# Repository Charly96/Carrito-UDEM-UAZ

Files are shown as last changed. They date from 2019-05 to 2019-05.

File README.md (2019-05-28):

# Carrito-UDEM-UAZ
Instrumentación, optimización estructural  y fabricación de vehículo con capacidades de autonomía a escala de bajo costo
Las piezas disponibles en este repositorio están en formato .prt, pero las disponibles en la carpeta .ige se encuentran en ese mismo formato para poder ser utilziadas en cualquier programa de CAD. 
Si se desea ensamblar, recomiendo leer el archivo ¨Repositorio¨ el cual indica paso a paso como hacerlo además de cuáles tornillos utilizar
###############################################

# Cart-UDEM-UAZ
Instrumentation, structural optimization and vehicle manufacturing with autonomy capabilities at a low cost scale
The pieces available in this repository are in .prt format, but the ones available in the .ige folder are in that same format to be used in any CAD program.
If you want to assemble, I recommend reading the file "Repository" which indicates step by step how to do it in addition to which screws to use

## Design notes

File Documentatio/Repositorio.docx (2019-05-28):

UNIVERSIDAD DE MONTERREY

ESCUELA DE INGENIERÍA Y TECNOLOGÍAS

Repositorio para elaborar y poner en marcha vehículo a escala con capacidades autónomas.

Asesor(es):

Antonio Martínez Torteya, Ph.D.

José María Celaya Padilla, Ph.D.

Integrantes:

Mauricio Delgado Vidal 339878 IMT

Carlos Arizpe Bautista 542800 IDA

Rodrigo Antonio García García 192376 IMT

San Pedro Garza García N.L, 24 de mayo del 2019

# Introducción

En este documento explicaremos cómo se realizó este vehículo y sus características y medidas para que pueda ser replicado, o bien se podría modificar si el usuario quisiera. De igual manera explicaremos qué sensores utilizamos y recomendamos junto con sus posicionamientos, que estos también quedan al criterio del usuario para modificar si gusta

# Materiales

- 4 sensores infrarrojos keyence
- 6 sensores ultrasónicos
- 1 Raspberry pi 3 b+
- 1 cámara web
- 4 llantas marca Steren
- 2 motorreductores
- 1 puente H

## Tornillos

- Holder

Tornillo: M5 x 0.8 mm Thread, 45 mm Long ……………….X2

Tuerca: M5 x 0.8mm…………….X2

Battery Holder

Tornillo:M5x0.8mm,20mm long…….X2

Tuerca M5x0.8mm………2

- Raspberry

Tornillo: M2.5x0.45,25mm long……X2

Tuerca: M2.5x0.8mm…X2

- Motores Traseros

Tornillo: M3x0.5mm,40mm………X4

Tuerca: M3x0.5……….X4

- Base de sensores

Tornillo: M3x0.5mm,20 mm long……X14

Tuerca: M3x0.5mm,20mm log………X14

- Motor de dirección

Tornillo: M2.5,6mm long………X2

- Unión Lateral

Tornillo: M4, 6mm long….X4

# Diseño

El diseño del chasis consta de dos partes que sirven como la base donde se colocan todos los sensores, componentes electrónicos y elementos de sujeción.

En esta sección se incluirán solo los modelos creados y no los que se encontraron disponibles en Internet. Estos últimos se incluyen en otra sección más adelante.

# Dibujos mecánicos

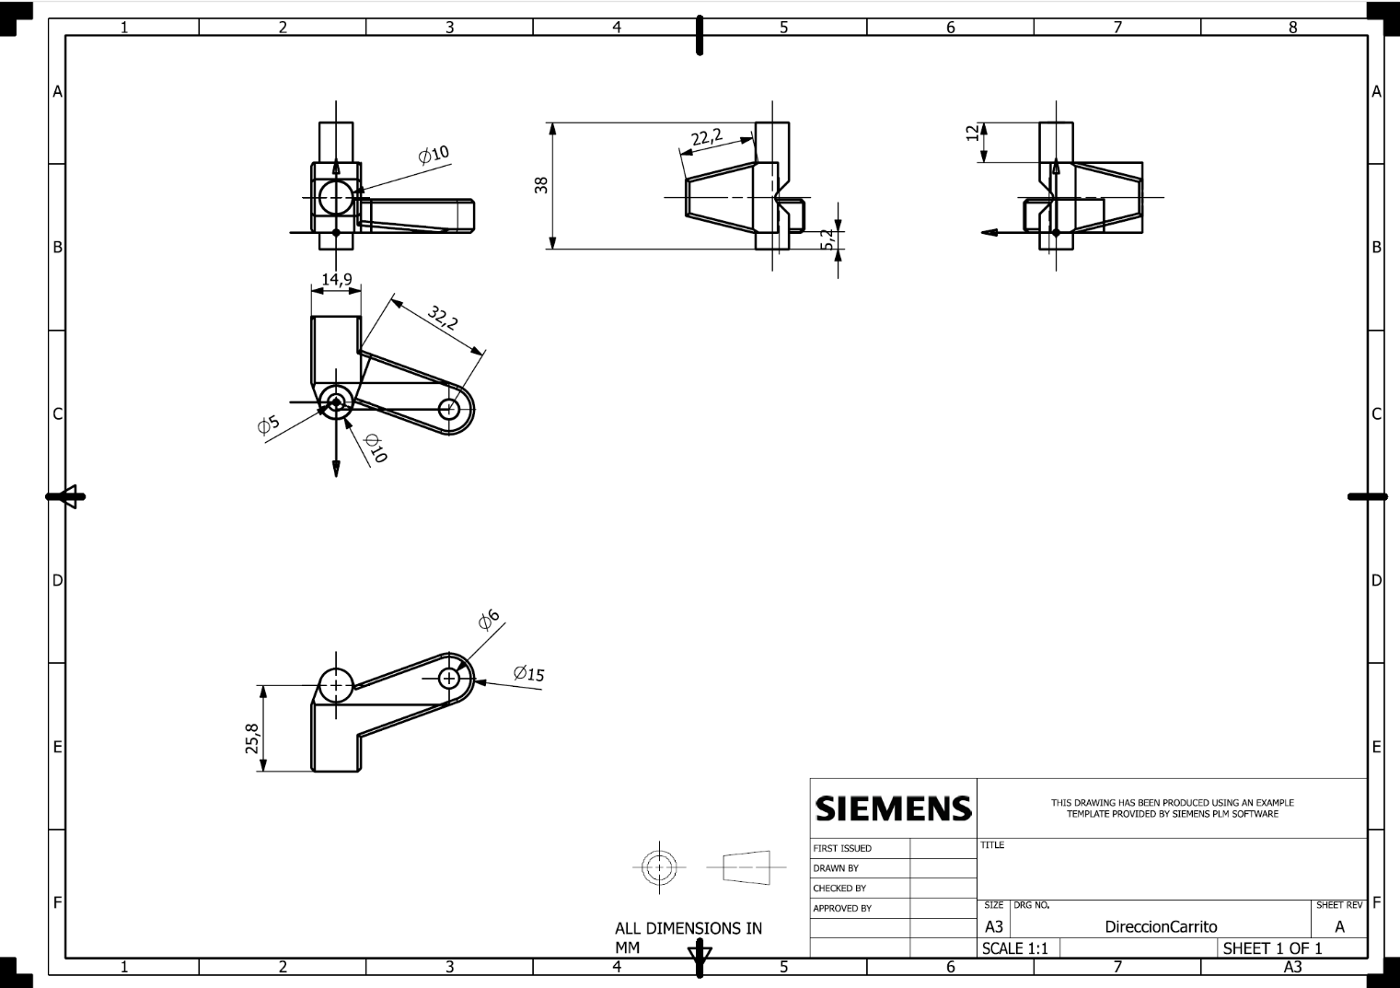
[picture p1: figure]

## Partes de Dirección

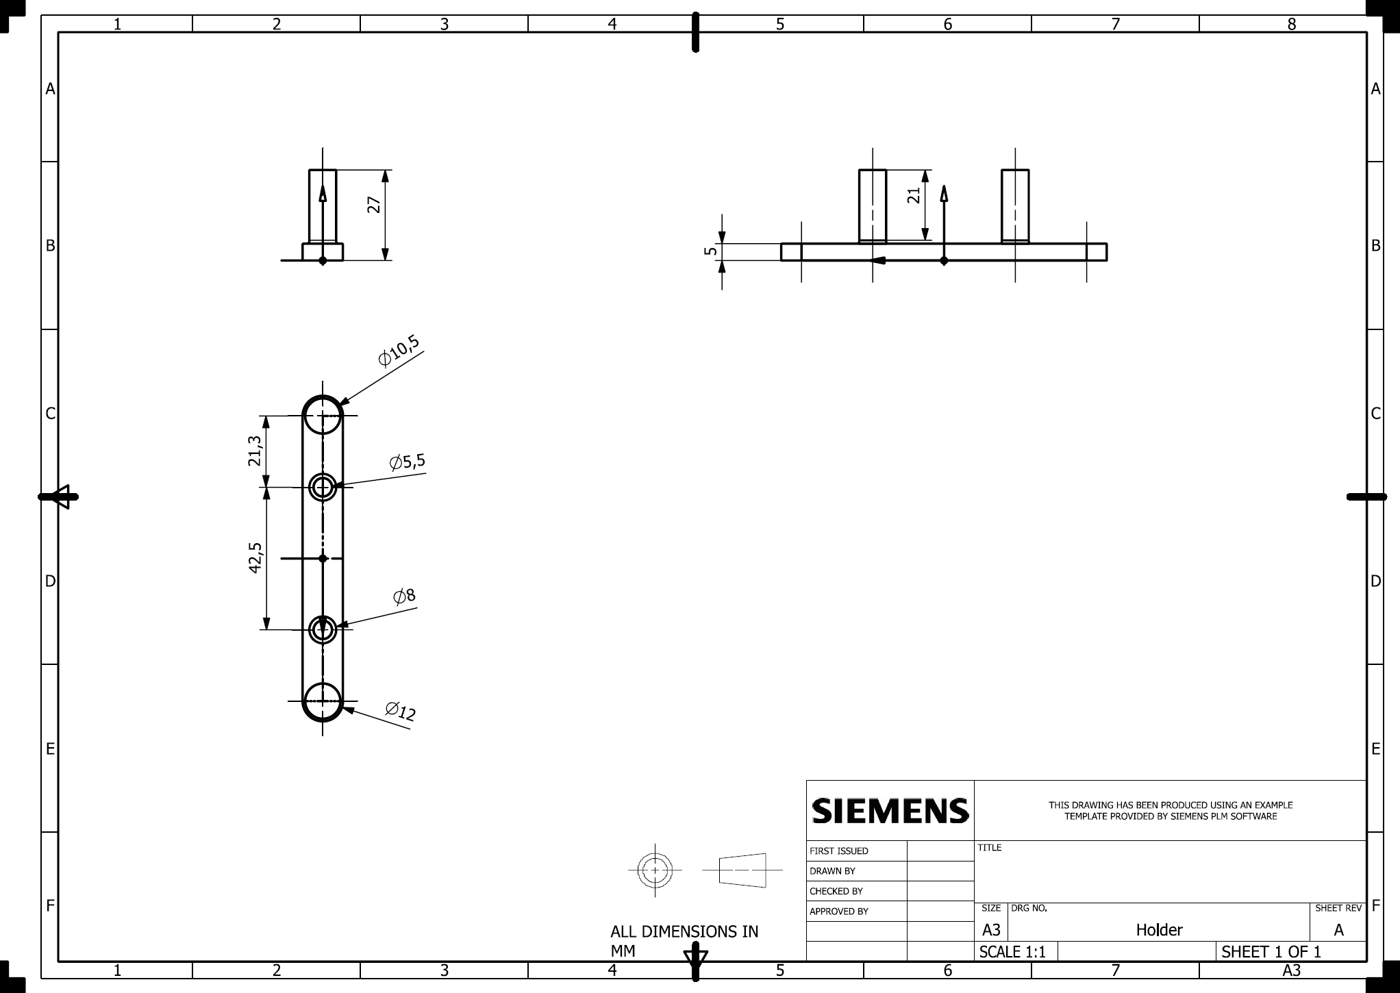
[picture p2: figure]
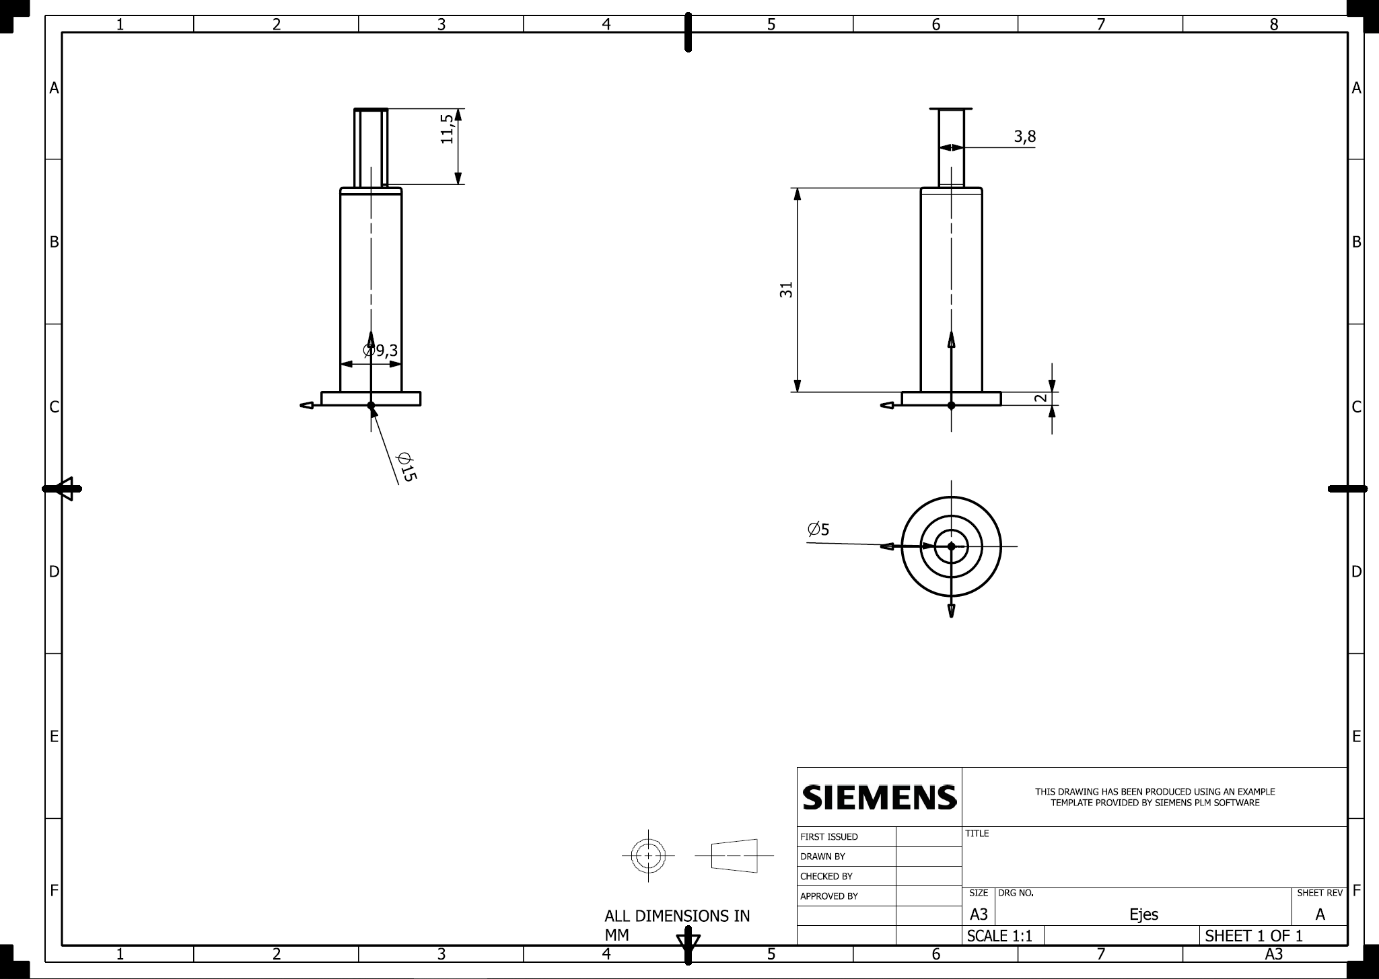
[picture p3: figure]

## Bases de sensores

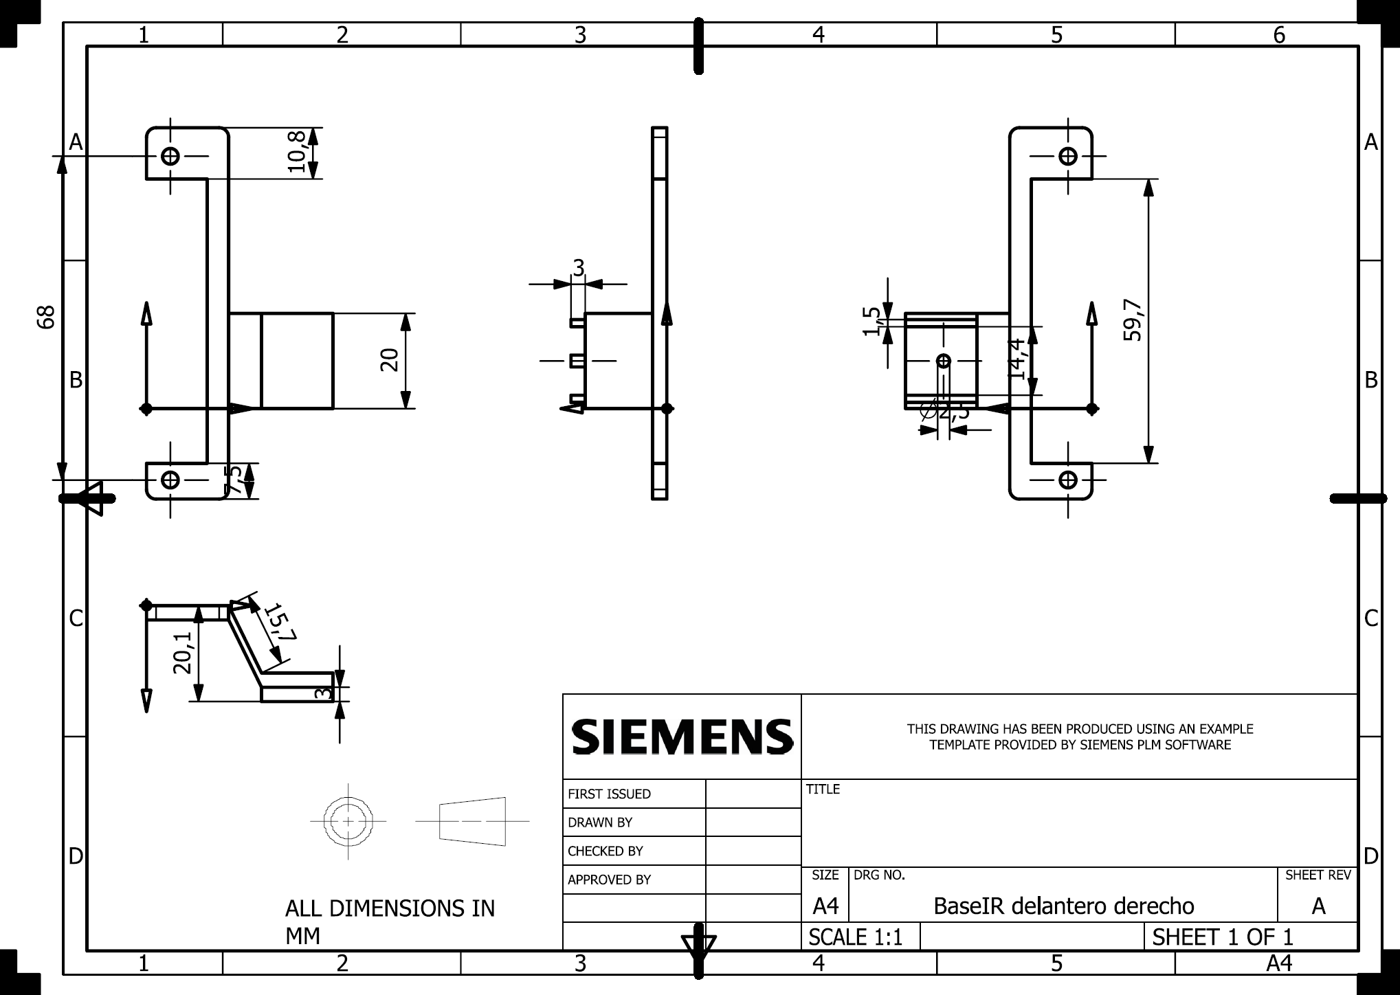
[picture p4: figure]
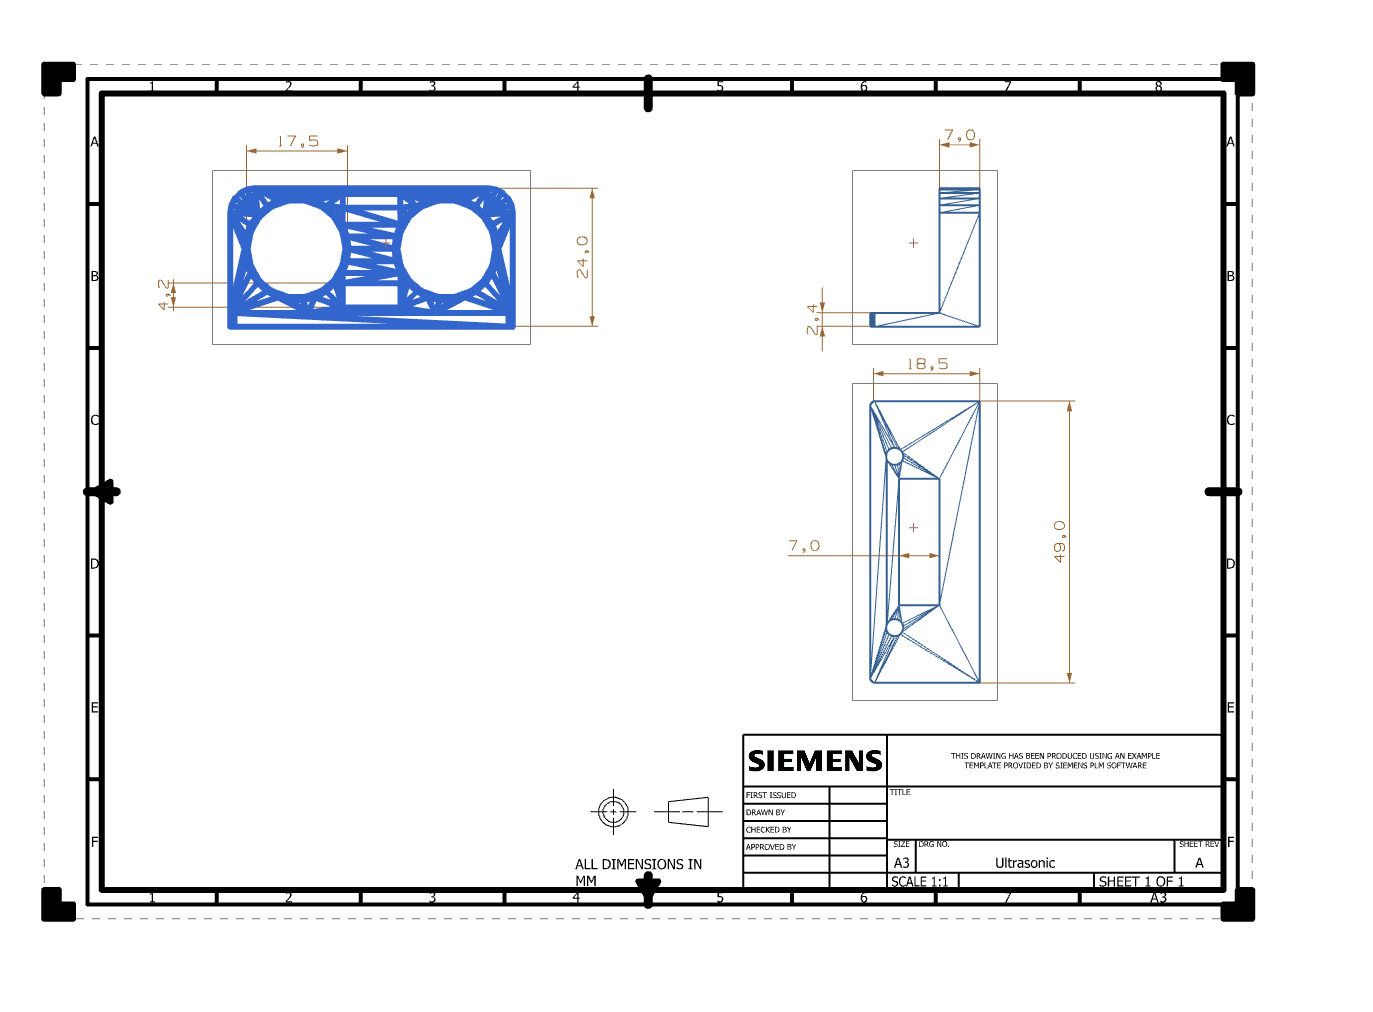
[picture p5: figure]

## Chasis

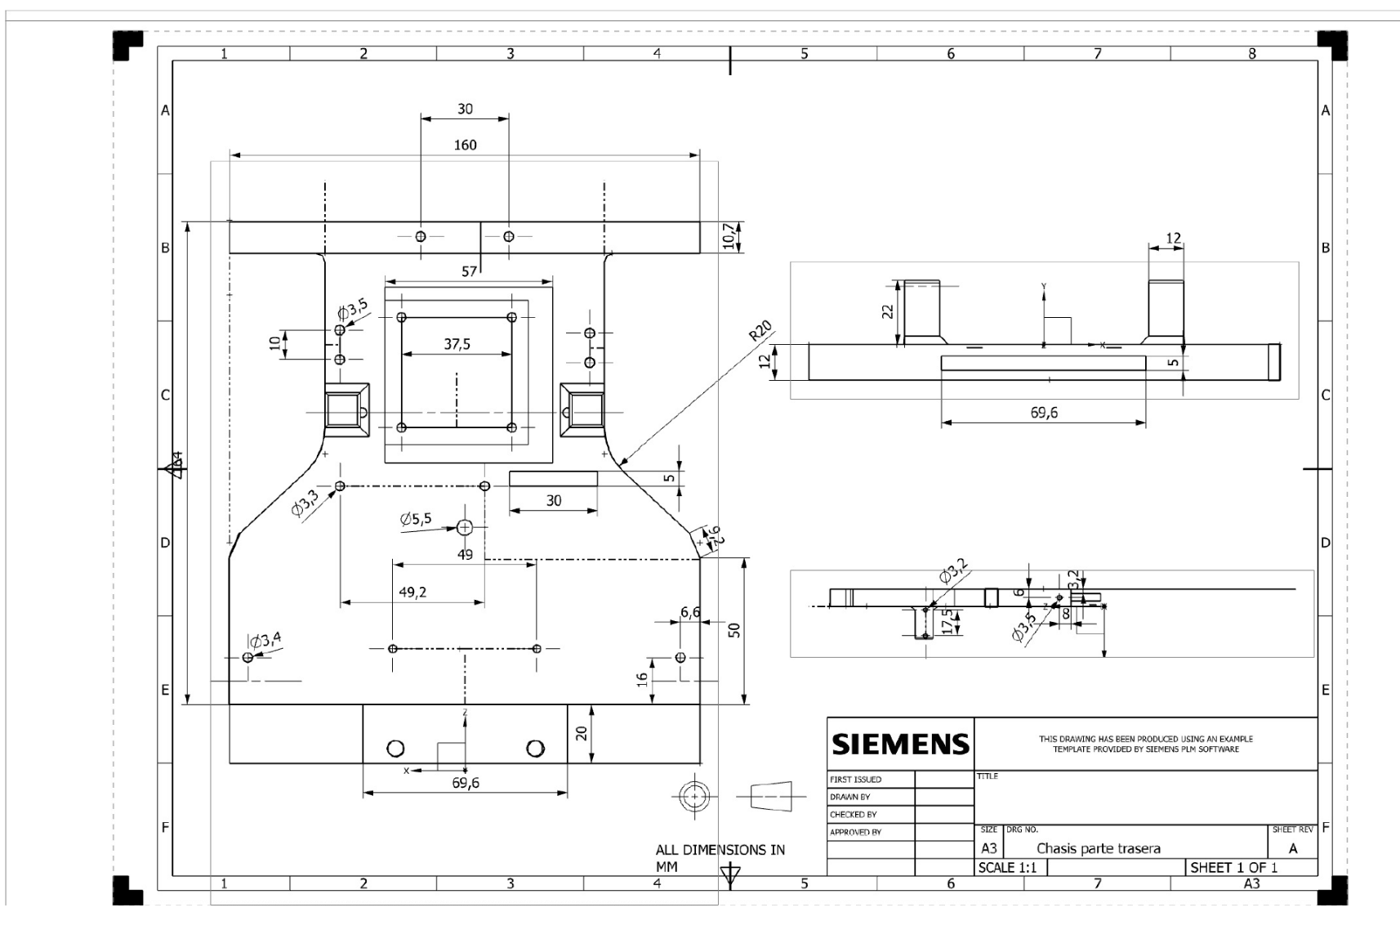
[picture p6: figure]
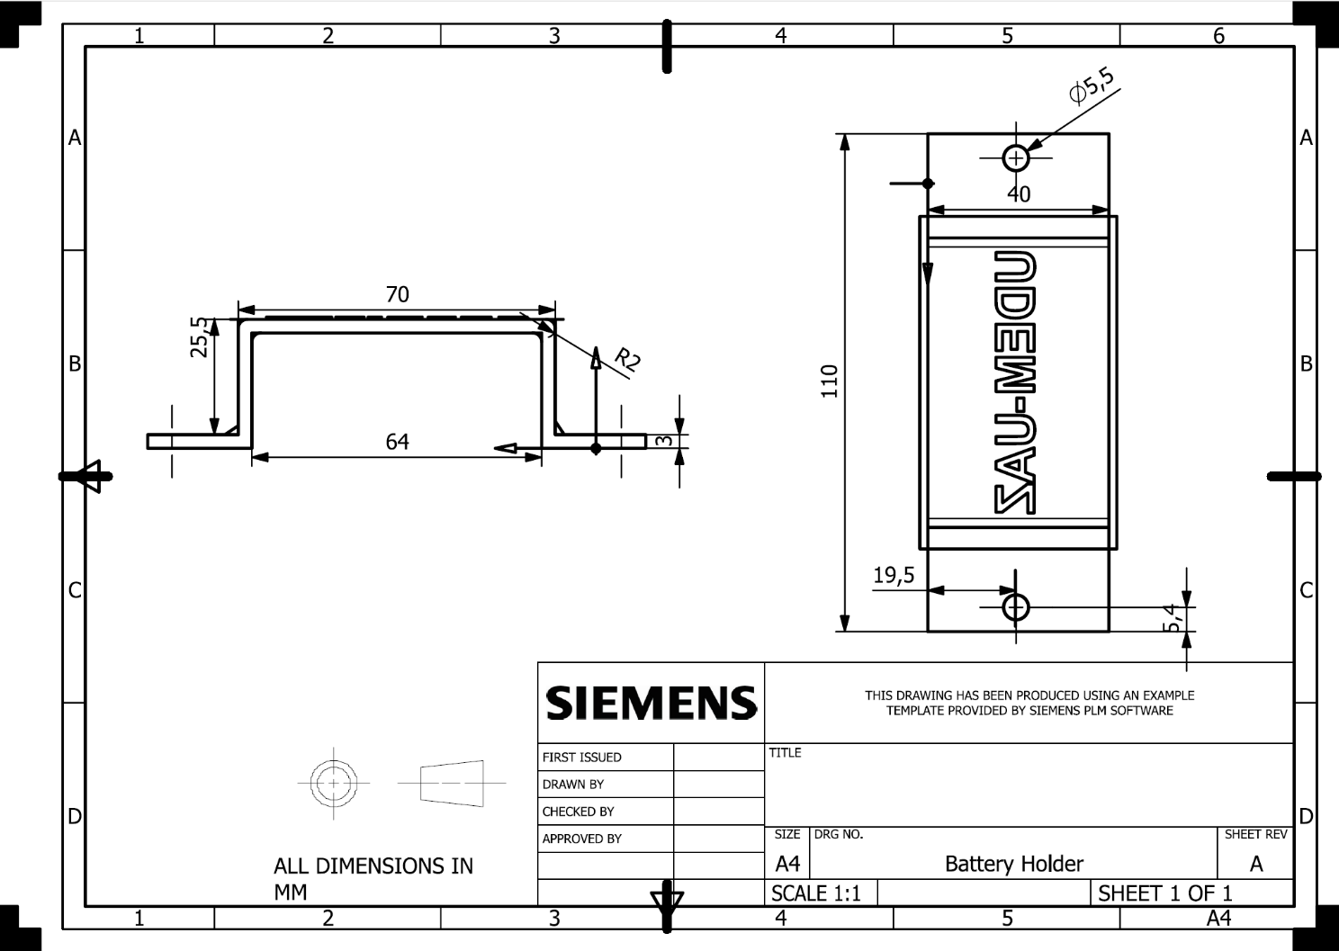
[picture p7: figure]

## Otros componentes

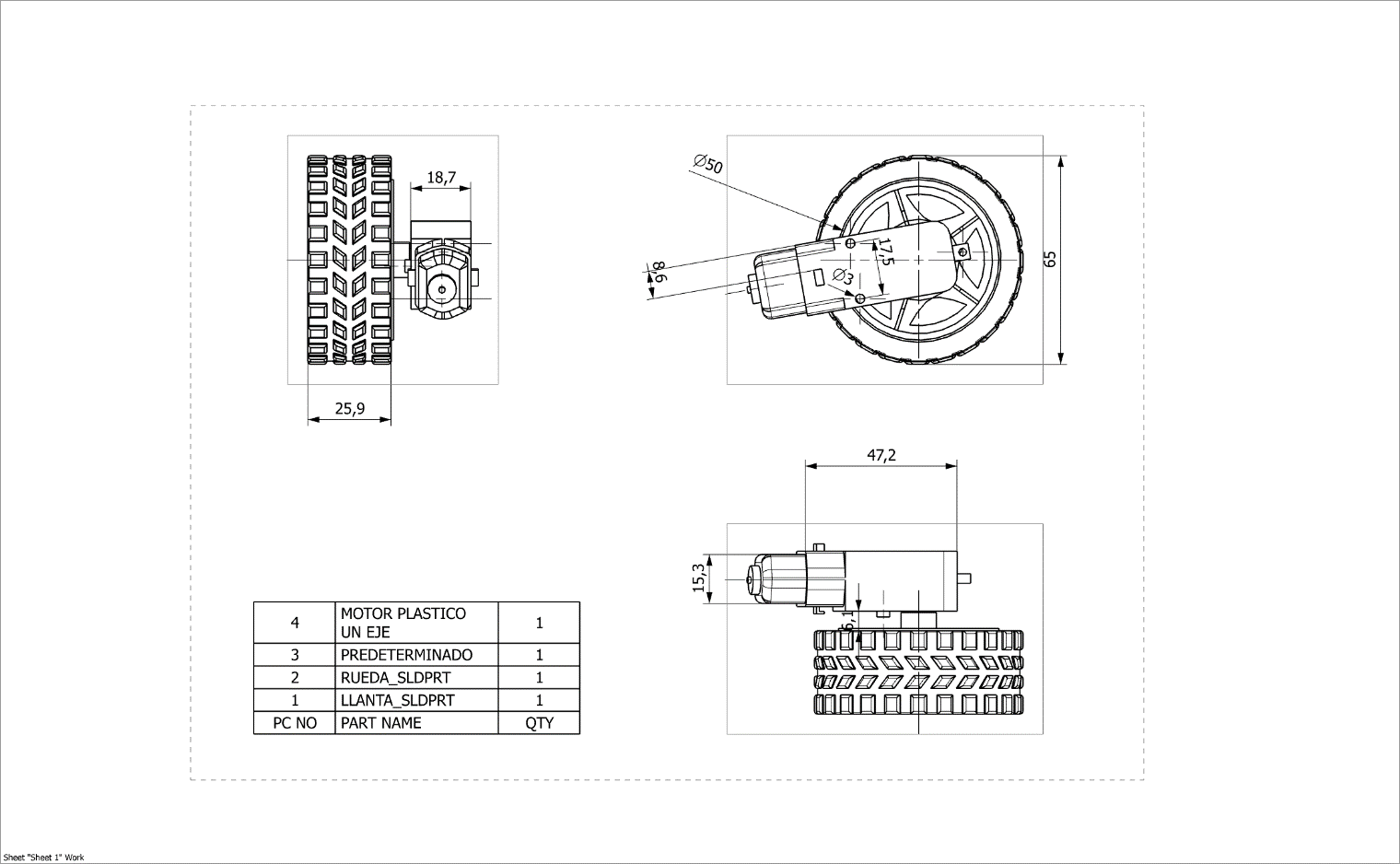
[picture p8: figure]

# Modelo de componentes electrónicos

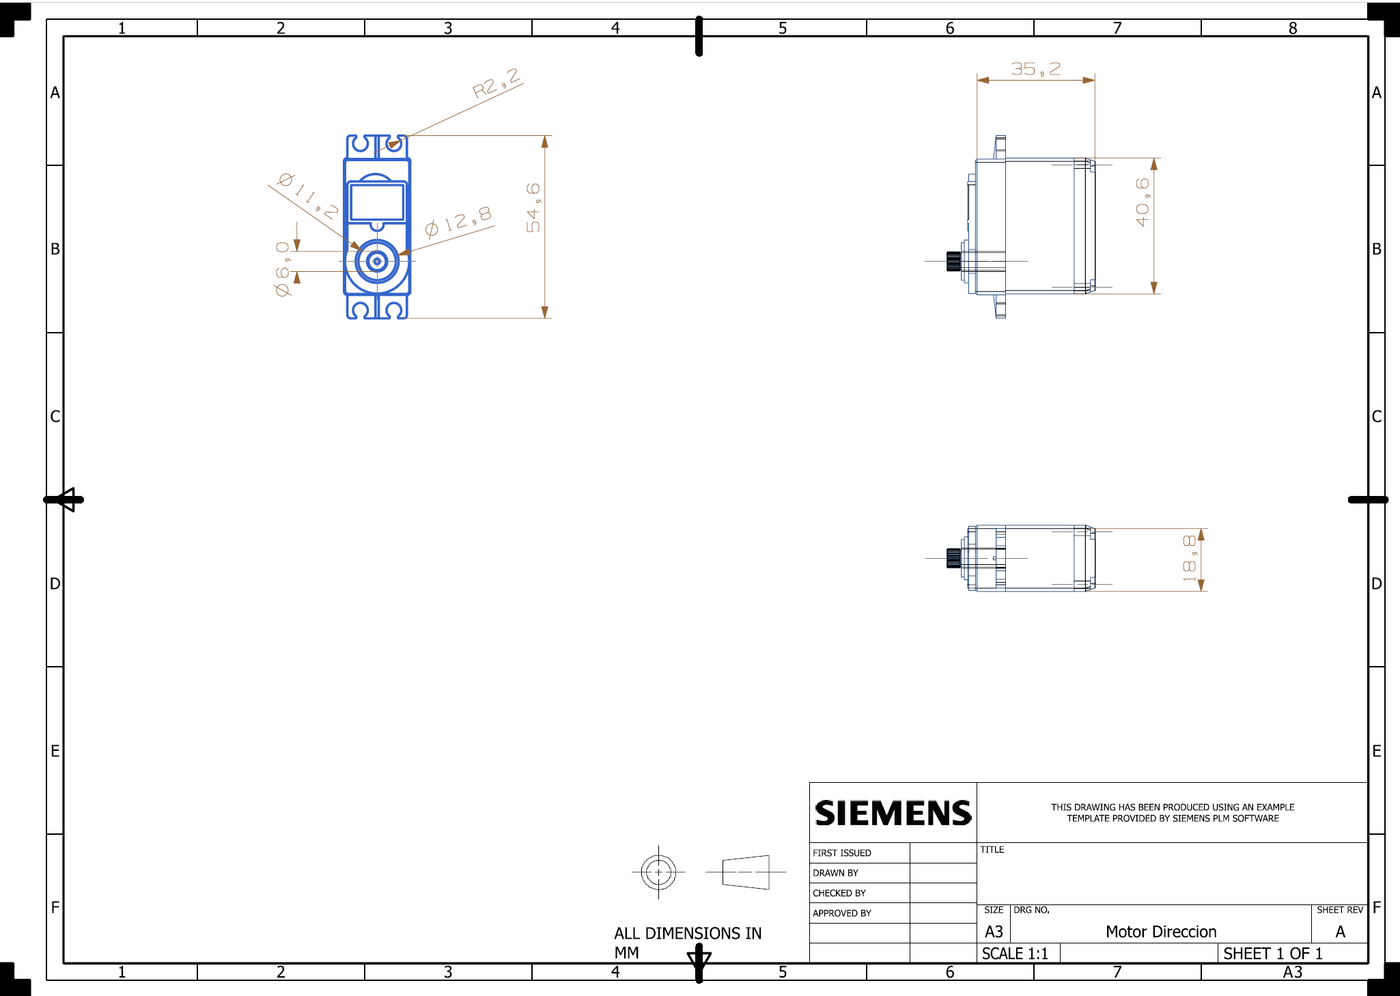
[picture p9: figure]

# Sugerencias de Sensores y posicionamientos

Los sensores que se utilizaron fueron ultrasónicos para la detección de obstáculos. Se utilizaron 3 sensores enfrente, 1 a cada lado y 1 en la parte trasera.

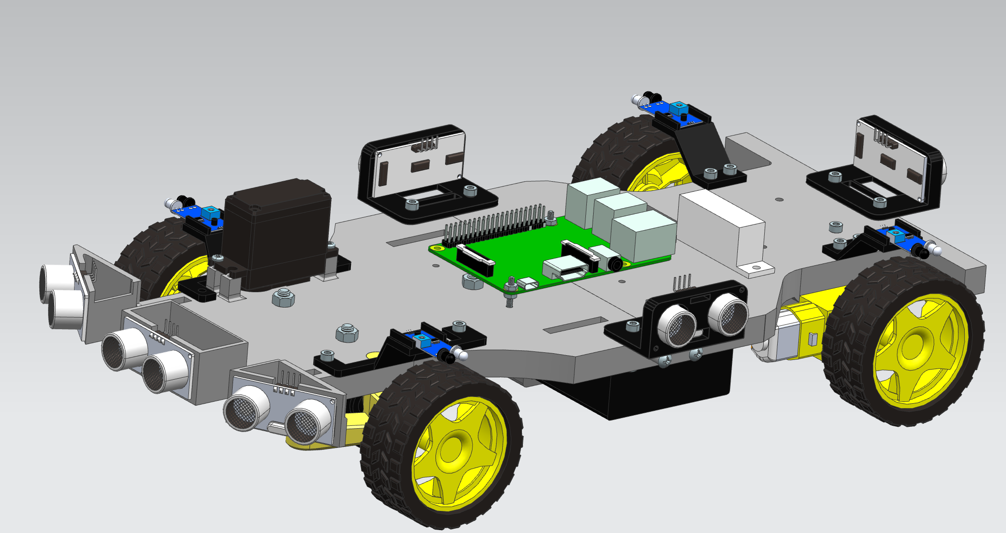
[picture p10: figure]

Para el estacionamiento en paralelo se sugiere utilizar sensores infrarrojos de presencia, esto porque no importa mucho saber la distancia entre los autos. Estos sensores se posicionaron en los ejes de cada llanta.

# Instrucciones de ensamblaje

Esta sección se dividirá en los diferentes pasos necesarios para el ensamble del carrito.

Paso 1

Unir las dos mitades del chasis

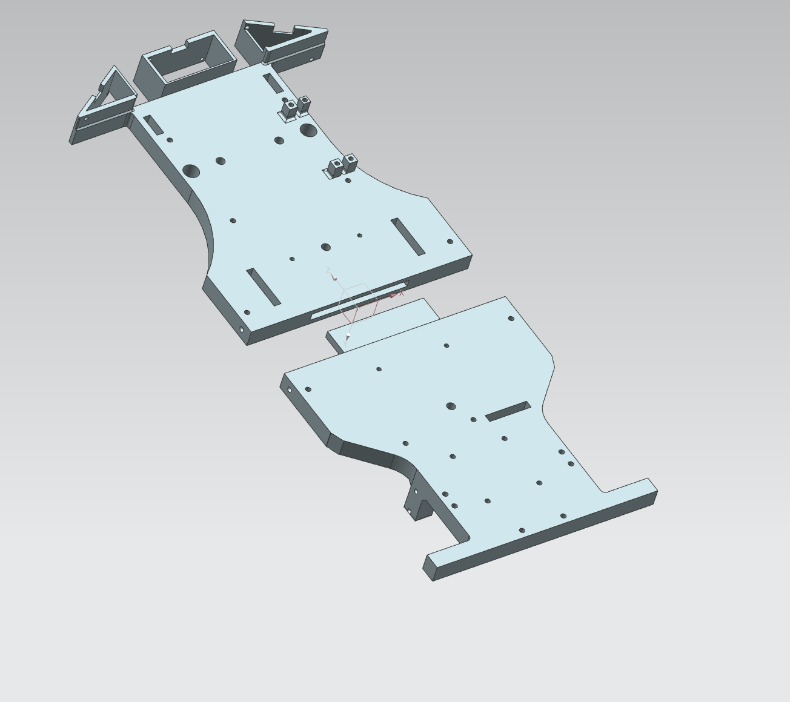
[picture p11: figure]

Paso 2

Colocar los soportes laterales para asegurar una mejor sujeción de los chasises.

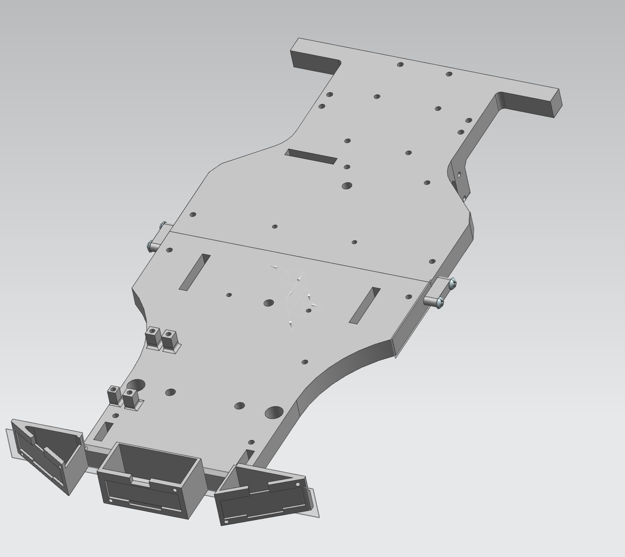
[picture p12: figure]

Utilizar Tornillo: M4, 6mm long

Paso 3

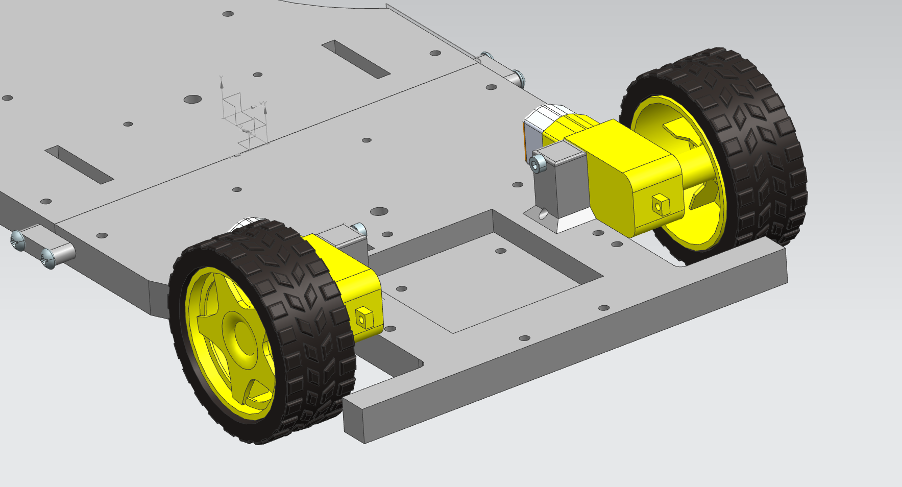
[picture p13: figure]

Colocar motores traseros.

Utilizar M3x0.5mm,40mm long con sus respectivas tuercas

Paso 4

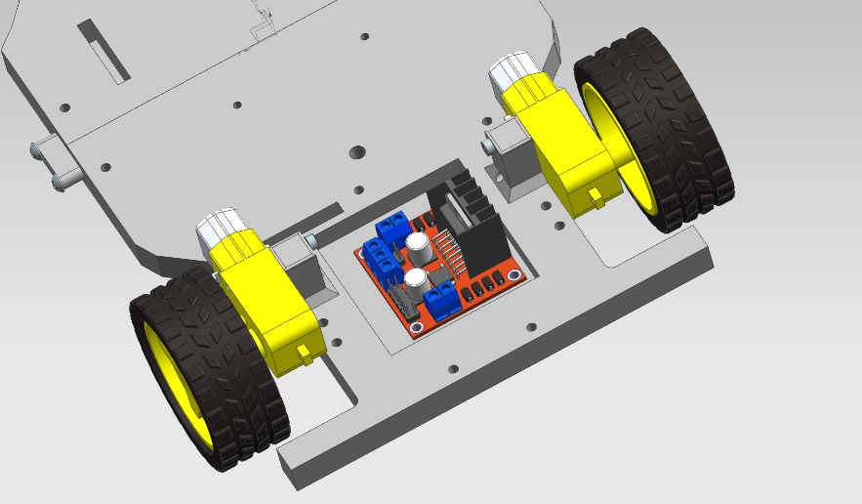
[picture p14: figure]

Colocar Puente H en medio de los motores traseros.

Utilizar Tornillos: M3x0.5mm, 20mm long

Paso 5

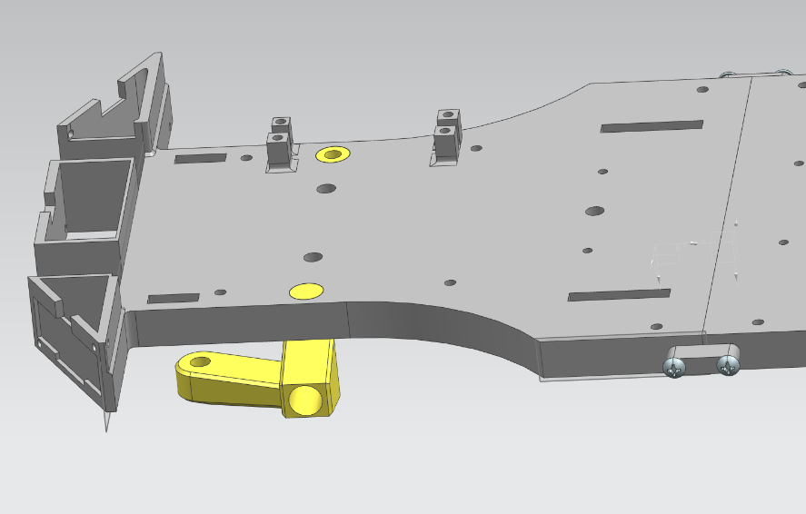
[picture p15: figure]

Colocar la pieza llamada: DirecciónCarrito en el lugar que se muestra en la foto.

*Asegurarse de colocar la pieza con el hueco del lado derecho.

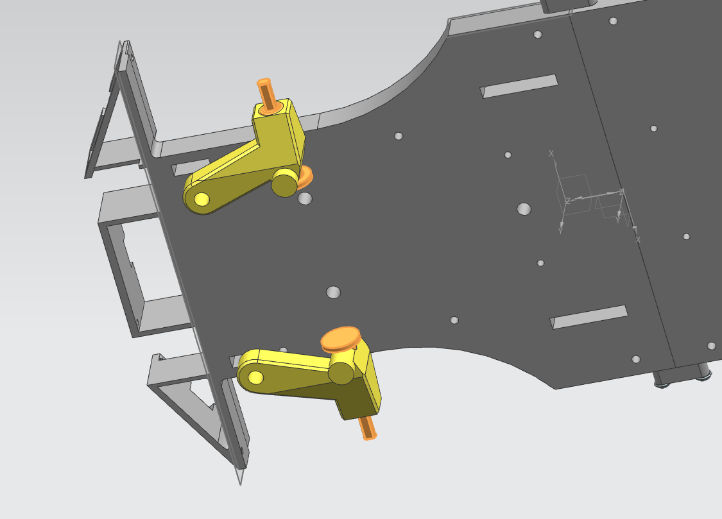
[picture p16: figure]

Paso 6

Colocar las piezas llamadas Ejes en donde se muestra en la figura.

*Precaución

La parte resaltada de esta pieza fue diseñada específicamente para que embonara al modelo de llanta que se utilizó.

En dado caso de cambiar de modelo de llanta, verificar si cuenta con el mismo tamaño.

En caso contrario, es solo cuestión de modificar la pieza del CAD llamada ¨Ejes¨ a la medida necesaria y se resolverá tal problema.

Al colocar las piezas ¨Ejes¨ en ¨DirecciónCarrito¨ en algunas ocasiones será necesario pulir un poco las piezas; esto debido a la manera en que las impresoras imprimen piezas circulares. Generalmente para crear un círculo con muchas caras planas que al colocarlas muy cercanas una tras otras simula un círculo, el detalle de esto es que se puede dejar bordes que aumentan la fricción entre piezas y afectan las tolerancias preestablecidas.

Se recomienda utilizar un Dremmel para eliminar estos bordes, tener cuidado de no pulir demasiado ya que esto haría que las piezas terminen más holgadas de lo deseado.

Paso 7

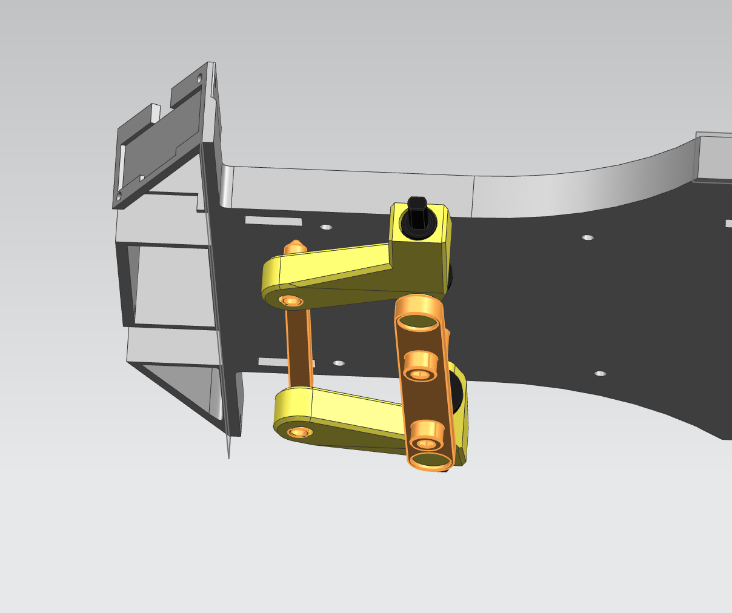
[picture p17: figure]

Ensamblar las piezas restantes de la dirección: Draglink y Holder.

Utilizar los tornillos: M5x0.8mm,45mm long con sus respectivas tuercas.

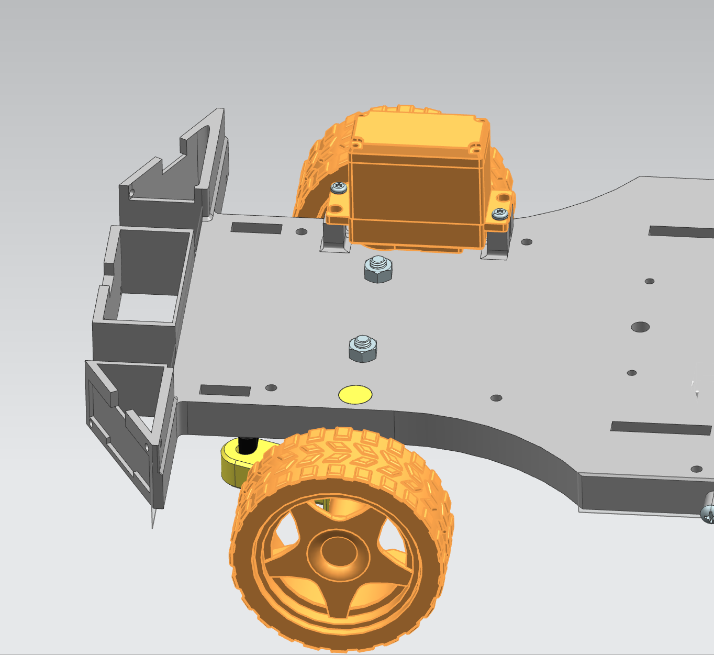
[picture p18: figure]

Paso 8

Ensamblar las ruedas delanteras y colocar el motor de la dirección como se muestra en la figura

Utilizar los tornillos: M2.5,6mm long

*Precaución

El piñón del motor de la dirección tiene que embonar lo suficientemente justo para poder mover la dirección, la medida establecida en el CAD debería de ser la correcta, pero, por cuestiones de material de impresión las tolerancias pueden no ser respetadas.

En caso de tener problemas al momento de montar el motor, modificar piezas ¨DirecciónCarritoDerecho¨. Esta pieza solo contiene el lado derecho de la pieza la cuál es la necesaria modificar para que el motor embone correctamente.

Paso 9

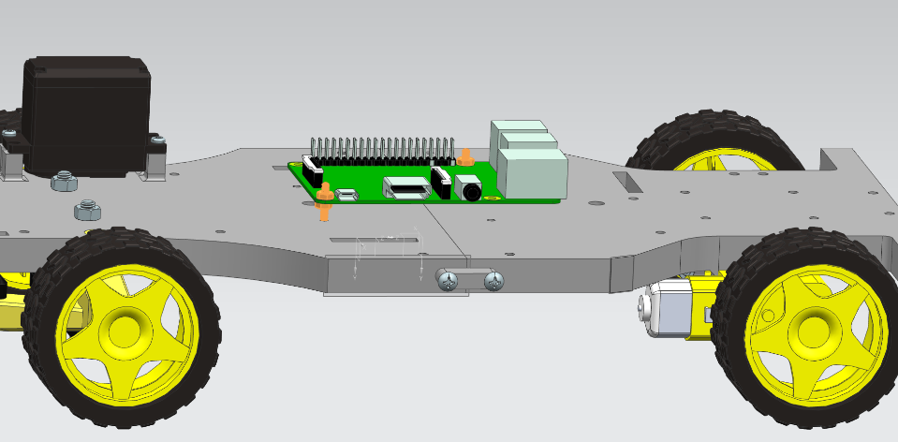
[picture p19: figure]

Colocar Raspberry en el centro del chasis.

Utilizar los tornillos M2.5x0.45,25mm long con sus respectivas tuercas.

Paso 10

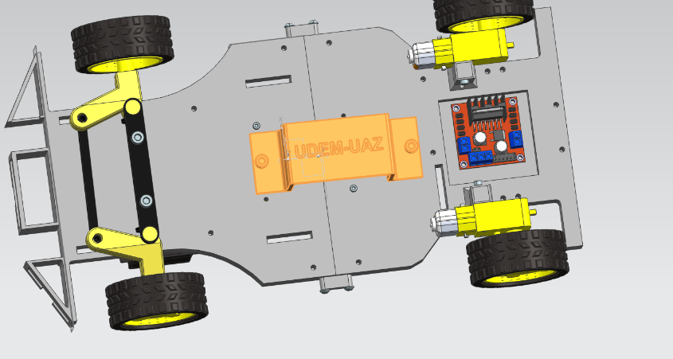
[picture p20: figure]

Ensamblar la pieza llamada Battery Holder como se muestra en la figura.

Utilizar los tornillos M5x0.8,20mm long con sus respectivas tuercas

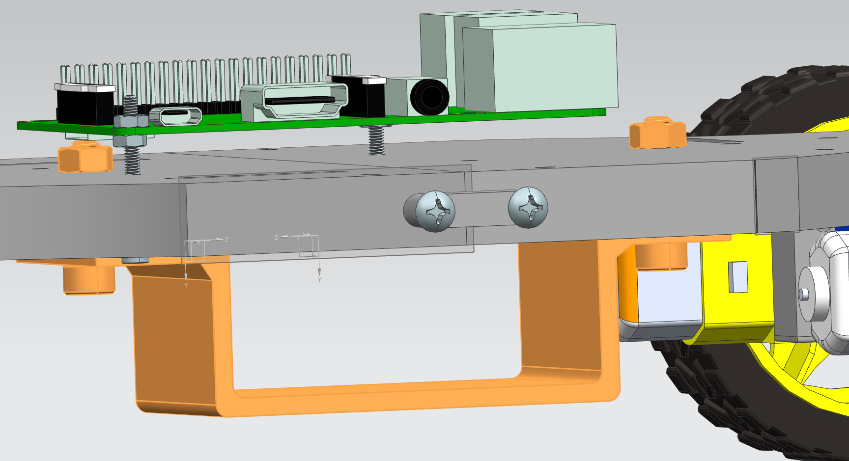
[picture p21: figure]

*Tener cuidado de no dañar la Raspberry con el tornillo del Battery Holder. Dejar una separación entre estos.

Paso 11

Todas las bases de los sensores Infrarrojos y Ultrasónicos se aseguran con el mismo tornillo M3x0.5mm,20mm long y su respectiva tuerca.

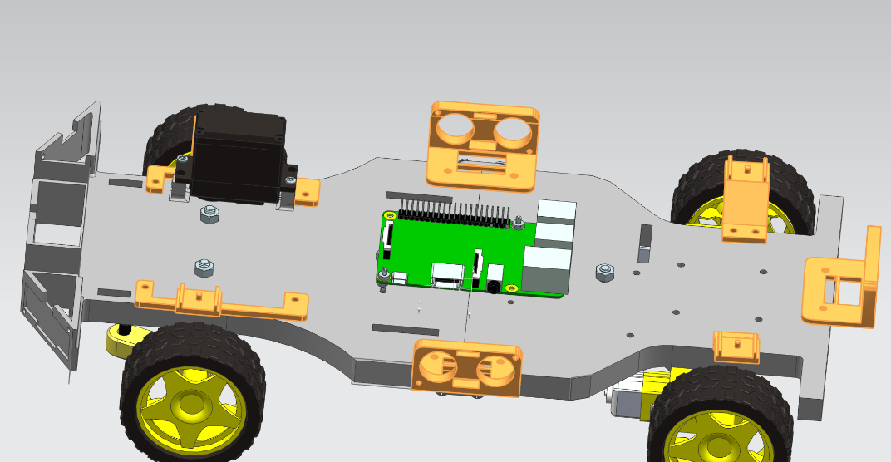
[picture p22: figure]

Colocar los sensores en las posiciones indicadas y con los tornillos mencionados.

Paso 12

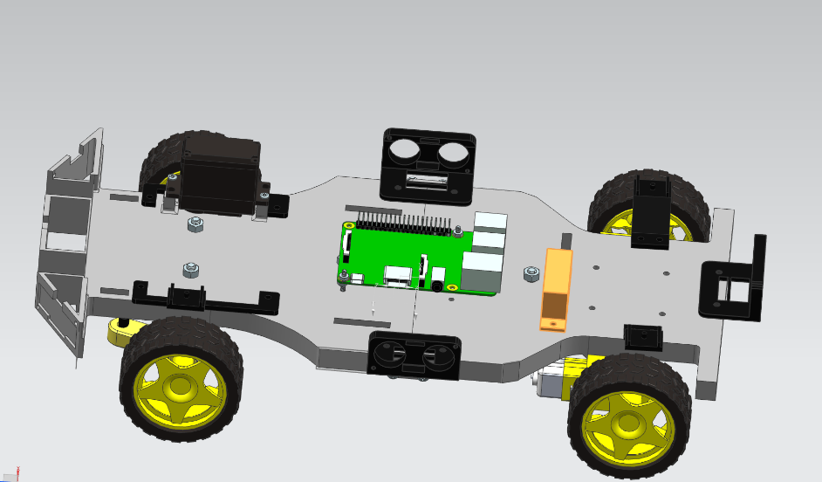
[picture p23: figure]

Colocar el Camara Holder en donde se indica en la foto. Utilizar tornillos M3x0.5,20mm long y sus respectivas tuercas.

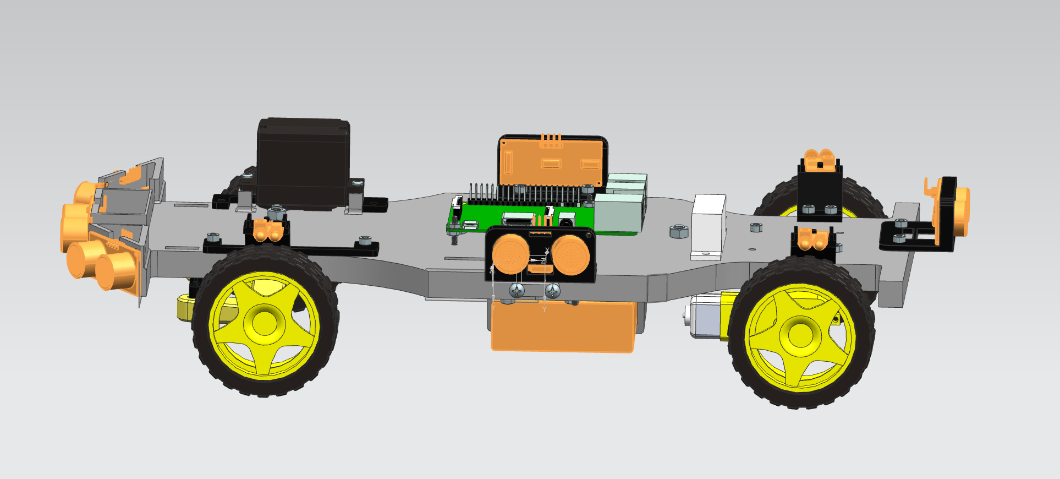
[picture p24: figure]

Por último, coloque los sensores y la batería en sus respectivas bases.

Es aconsejable en dado caso que no se consigan los tornillos para sujetarlos, utilizar silicón para asegurarlos a su base.

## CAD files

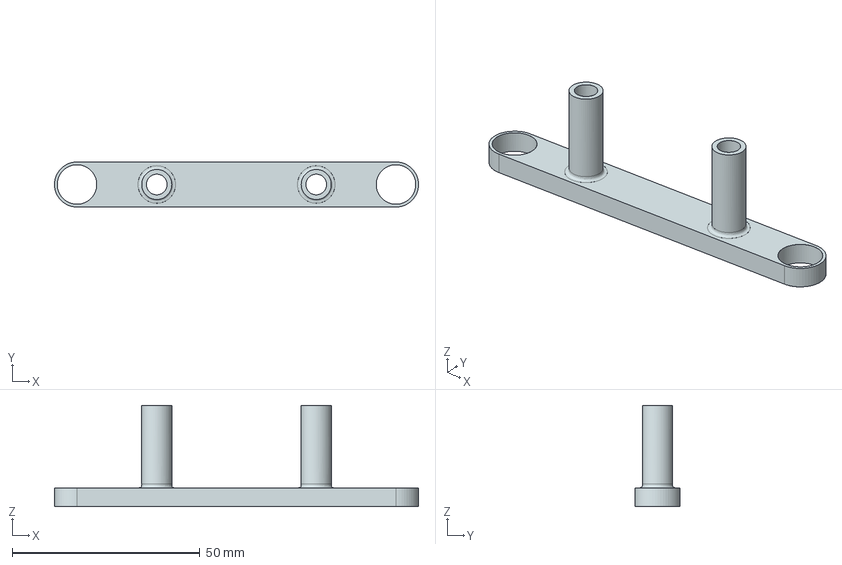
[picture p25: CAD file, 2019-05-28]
.igs/Holder.prt.igs
97.0 x 12.0 x 27.0 mm

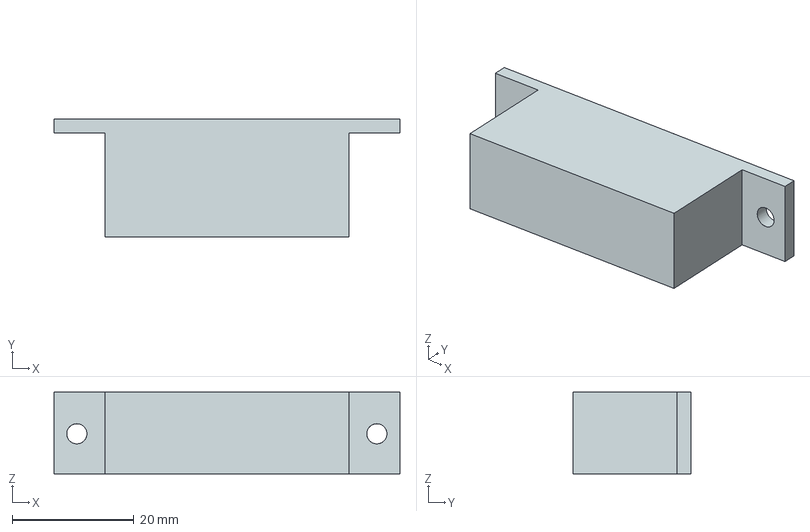
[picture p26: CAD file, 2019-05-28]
.igs/holder camara.prt.igs
56.8 x 19.4 x 13.4 mm

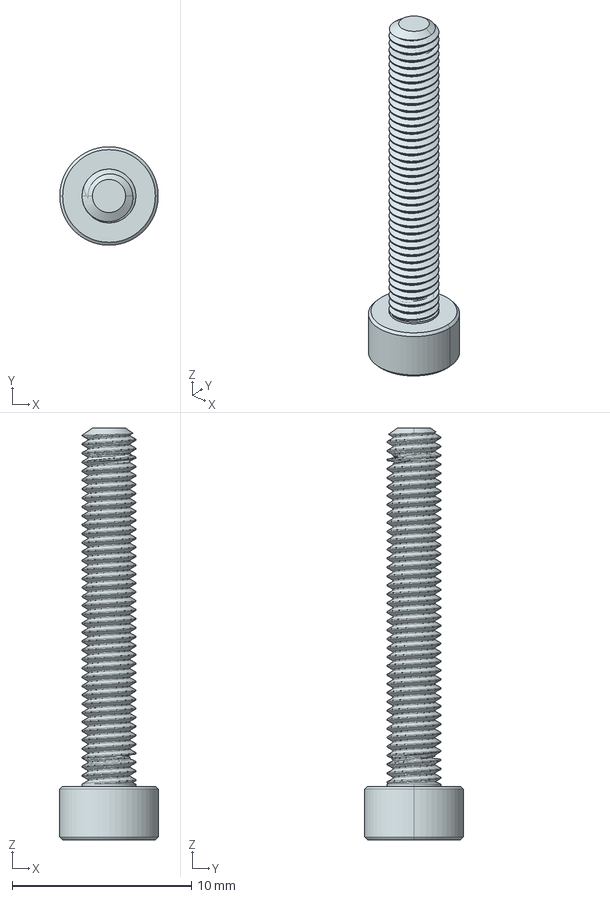
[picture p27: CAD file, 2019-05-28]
.igs/Tornillo M3x0.5,20mm.igs
5.50 x 5.50 x 23.0 mm

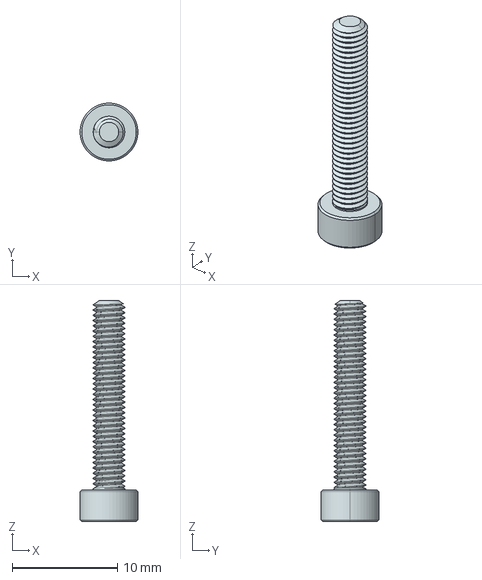
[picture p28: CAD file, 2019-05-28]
.igs/Tornillo Base de Sensores M3x0.5,18mm.igs
5.50 x 5.50 x 21.0 mm

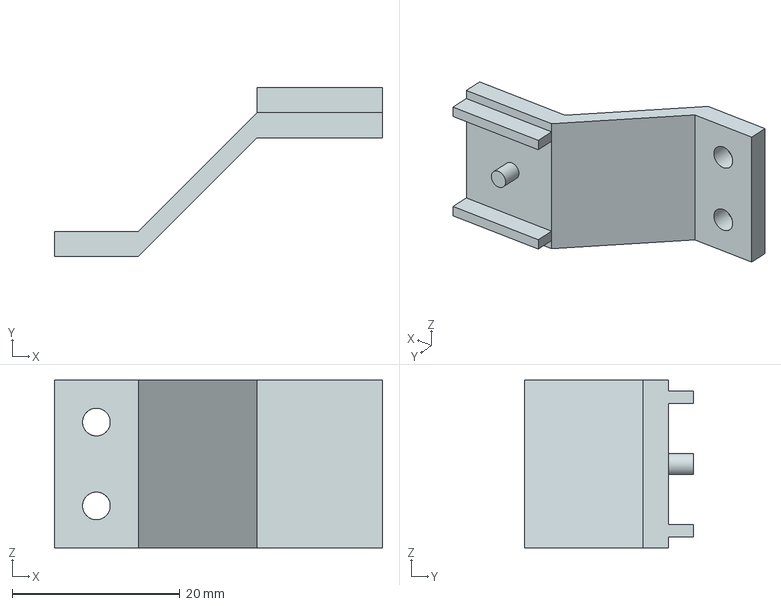
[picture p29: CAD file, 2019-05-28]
.igs/BaseIR.prt.igs
39.1 x 20.1 x 20.0 mm

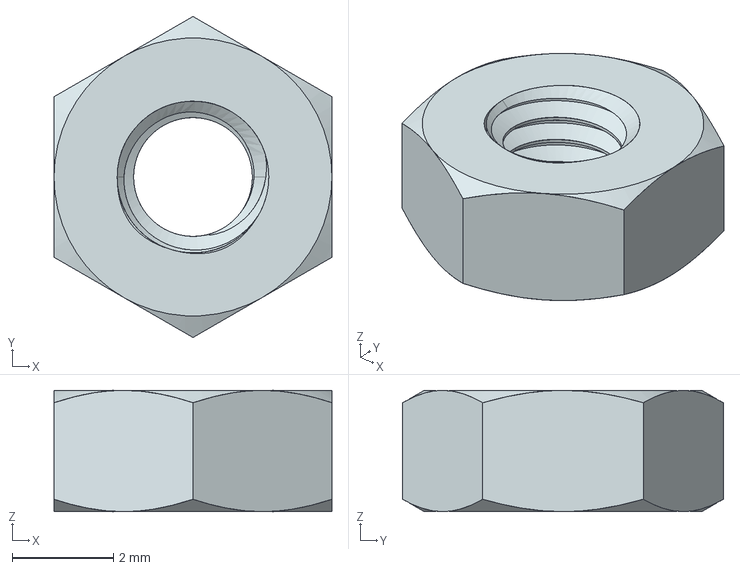
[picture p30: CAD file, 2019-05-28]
.igs/Tuerca M3x0.5.igs
5.50 x 6.35 x 2.40 mm

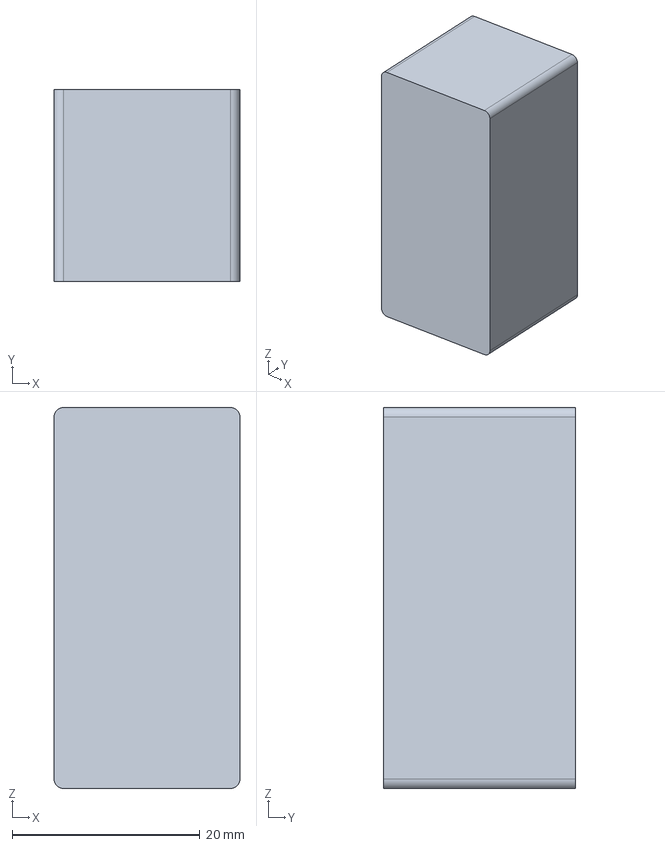
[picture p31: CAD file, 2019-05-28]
.igs/Medio_1.prt.igs
19.8 x 20.5 x 40.6 mm

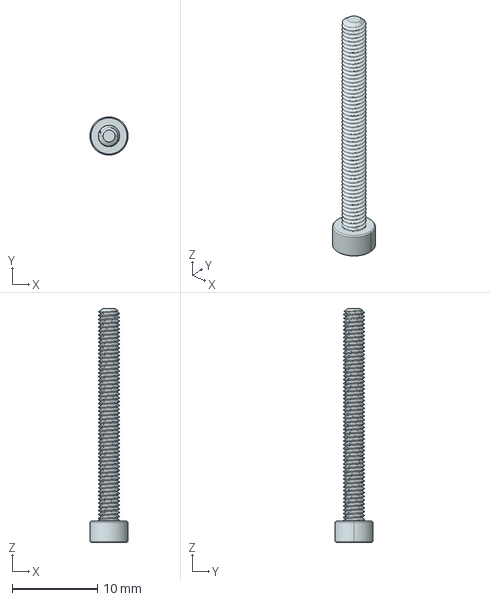
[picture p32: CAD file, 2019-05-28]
.igs/Torinllo Raspberry M2.5x0.45,25mm.igs
4.50 x 4.50 x 27.5 mm

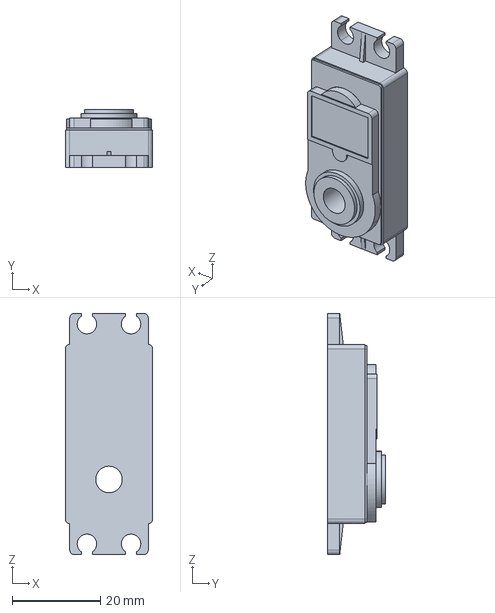
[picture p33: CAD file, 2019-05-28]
.igs/Top_1.igs
19.8 x 13.2 x 54.6 mm

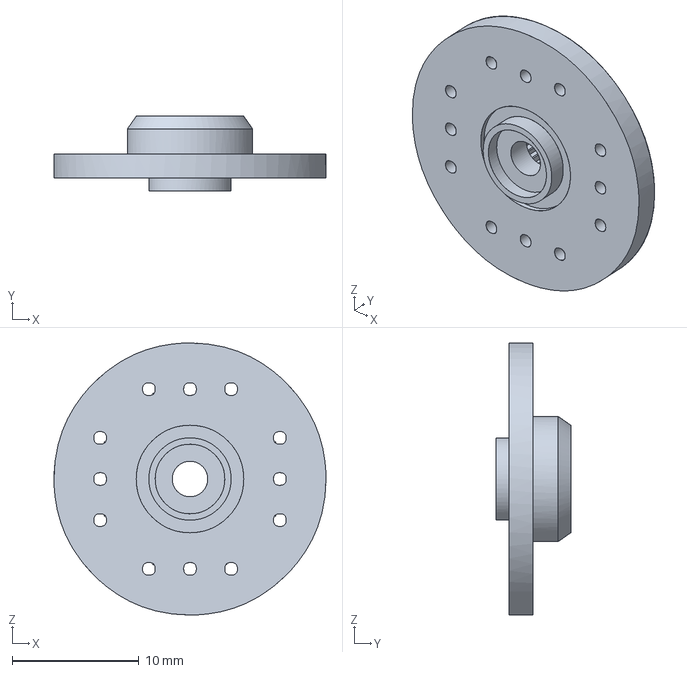
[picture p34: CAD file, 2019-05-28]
.igs/Acople circular_1.igs
21.5 x 5.90 x 21.5 mm

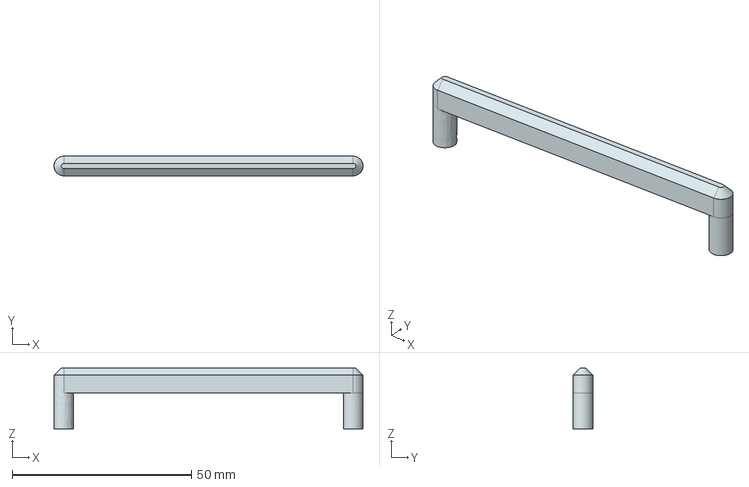
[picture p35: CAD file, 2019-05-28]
.igs/DragLink.prt.igs
86.3 x 5.50 x 17.0 mm

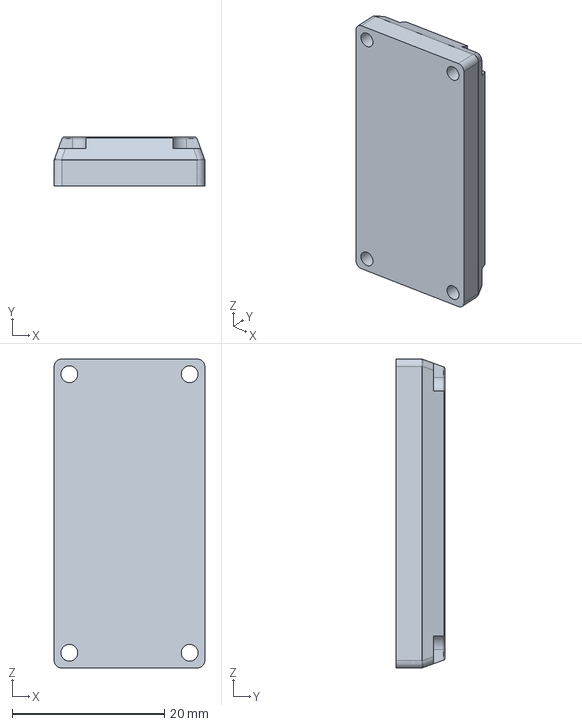
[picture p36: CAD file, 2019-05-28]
.igs/Base_1.prt.igs
19.8 x 6.40 x 40.6 mm

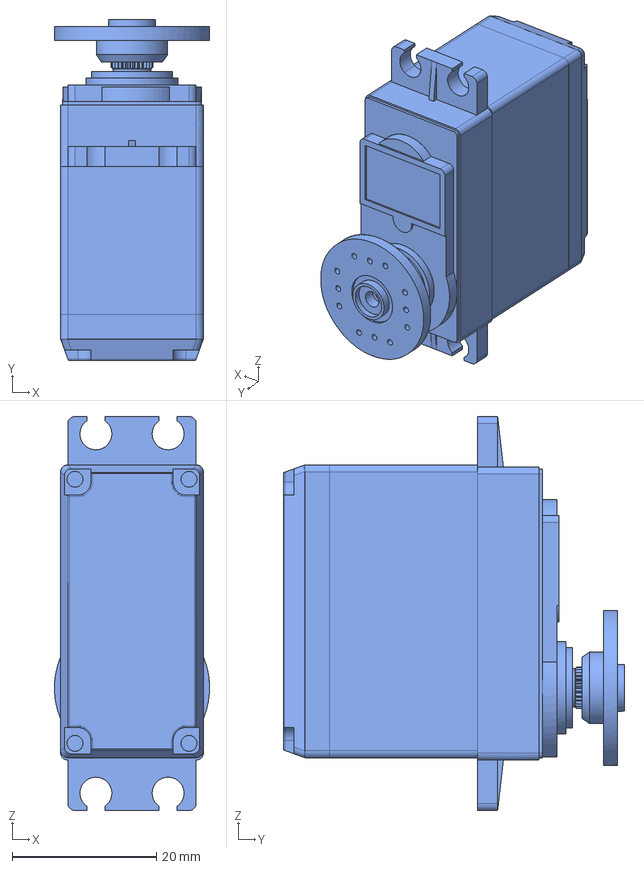
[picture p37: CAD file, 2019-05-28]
.igs/MG_996R_step.prt.igs
21.5 x 47.3 x 54.6 mm

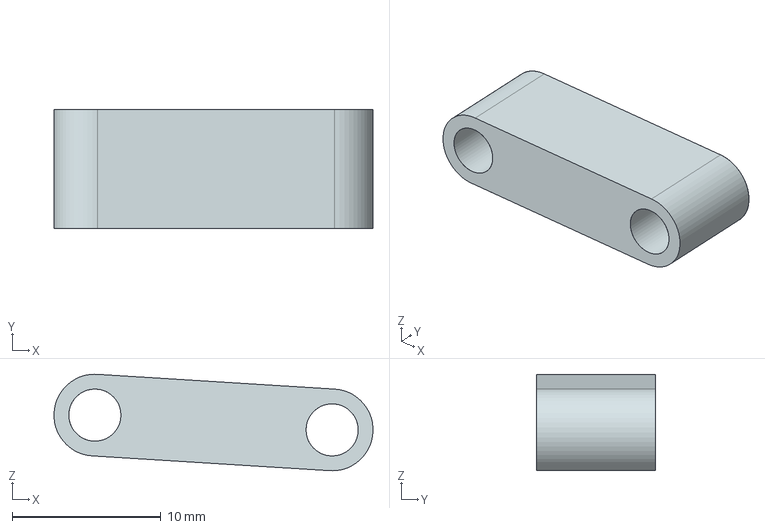
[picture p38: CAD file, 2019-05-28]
.igs/Soporte Unión Chasis.igs
21.5 x 8.00 x 6.50 mm

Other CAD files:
.igs/Ultrasonic holder.igs
.igs/Battery Holder.prt.igs
.igs/Tornillo Holder M5 x 45mm.igs
.igs/Tornillo Motor de dirección M2.5, 6mm long.igs
.igs/BaseIR delantera doble.prt.igs
.igs/BaseIR delantero derecho.prt.igs
.igs/BaseIR delantero izquierdo.prt.igs
.igs/Battery.prt.igs
.igs/Chasis parte trasera corregida 3.prt.igs
.igs/Chasis.prt.igs
.igs/DireccionCarrito.prt.igs
.igs/Eje_1.prt.igs
.igs/Ejes.prt.igs
.igs/H Bridge.prt.igs
.igs/HEX NUT M3x2.4mm.prt.igs
.igs/IR sensor.prt.igs
.igs/M3x 0.5mm Tornillo Holder.prt.igs
.igs/Predeterminado.igs
.igs/Raspberry.igs
.igs/Rueda_sldprt.igs
.igs/SOCKET HEAD SCREW M3X0.5.15mm.prt.igs
.igs/Tornillo Battery Holder M5x0.8mm, 20mm.igs
.igs/Tornillo Motor trasero M3x0.5mm,30mm.igs
.igs/Tornillo Raspberry M2.5X0.45,16mm_step.igs
.igs/Tornillo Raspberry M2.5x0.45,15mm.igs
.igs/Tuerca Raspberry M2.5.igs
.prt/Acople circular_1.prt
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
